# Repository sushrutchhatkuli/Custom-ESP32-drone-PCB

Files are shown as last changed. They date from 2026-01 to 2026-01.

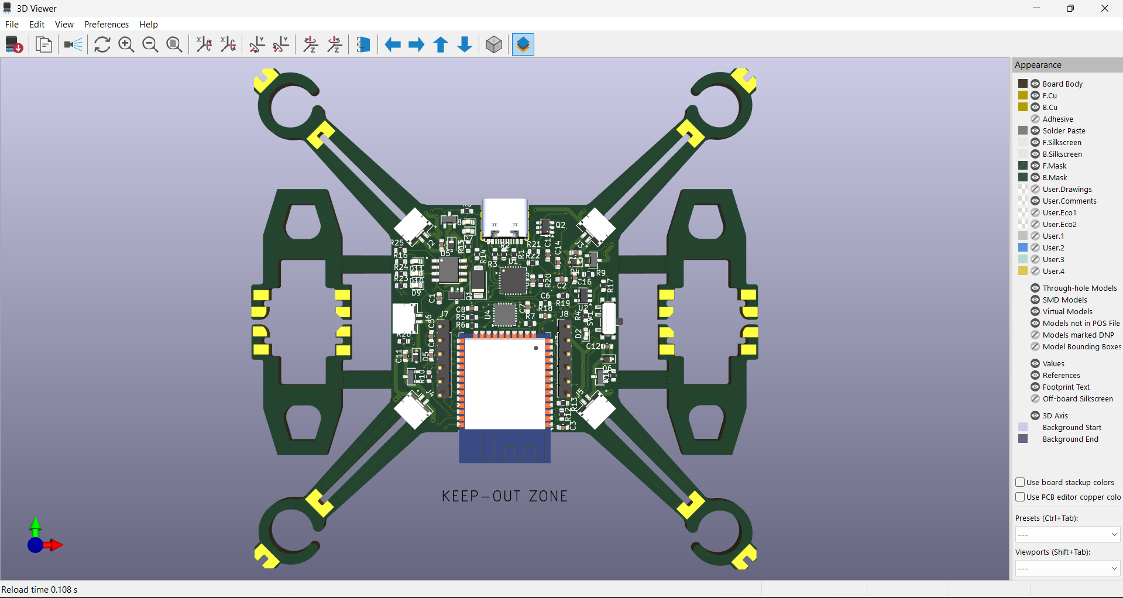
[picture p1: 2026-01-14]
Images/PCB Editor / 3D Views/Screenshot 2026-01-11 161916.png

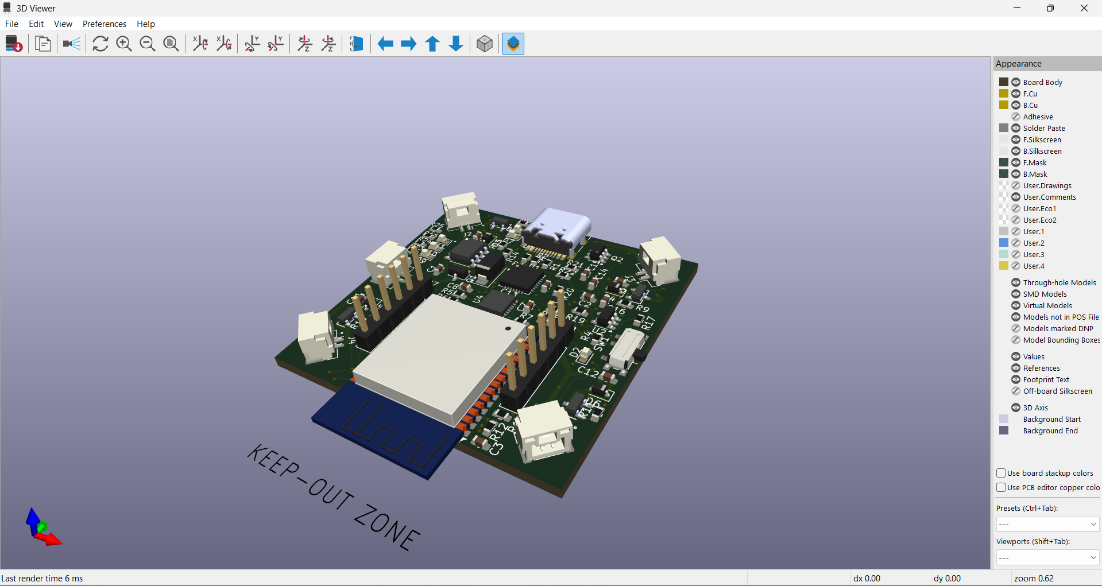
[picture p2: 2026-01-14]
Images/PCB Editor / 3D Views/Screenshot 2026-01-07 224814.png

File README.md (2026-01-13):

# Cheap Drone

I designed a custom drone flight controller PCB based on the ESP32-WROOM-32. The board uses USB-C charging, regulated 3.3 V power delivery, and onboard IMU sensing using the MPU-6050. The PCB is currently being fabricated, and I am actively working on automatic stabilization code for my motors.

## Overview
The goal of this project was to design a low-cost, custom flight controller PCB for a quadcopter drone while gaining hands-on experience with power management, embedded hardware design, and PCB layout. Instead of using a real controller, I wanted to use a free app that can be downloaded from the App store since ESP32 supports Wifi and Bluetooth.

The design is organized into three main parts:
- Power management
- ESP32 control and programming
- Motors and sensors

## Power Management
Power management was a major focus of this design. The board uses a battery charging circuit along with a voltage regulator to safely power all components. The incoming voltage is regulated to 3.3 V using the MIC5219-3.3YM5, which supplies power to both the ESP32 and the MPU-6050.

When the board is connected to USB-C, the voltage passes through a Schottky diode (SS34) and reaches the gate of an AO3401A P-channel MOSFET. This turns the MOSFET off and disconnects the battery (+VBatt) from the system, allowing the drone to run directly from USB power while the battery is charging.

Battery charging is handled by the TP4056, which safely manages the LiPo charging process. Two LEDs connected to the TP4056 indicate whether the battery is charging or fully charged. When the USB cable is unplugged, the MOSFET automatically turns on, reconnecting the battery so it can power the system. Decoupling capacitors are placed throughout the power rails to reduce noise and improve voltage stability.

## ESP32 Control and Programming
The +VBUS line is routed before the voltage regulator so it can supply 5 V power to the CP2102 USB-to-UART converter, which requires a higher voltage than the ESP32.

The USB data lines (D+ and D−) carry compiled code from the computer to the CP2102. The CP2102 converts this USB data into UART signals (TX and RX) that are sent to the ESP32. The RTS and DTR signals from the CP2102 pass through a 2N7002DW MOSFET, which automatically controls the EN and BOOT pins of the ESP32 during programming. This allows the ESP32 to enter firmware upload mode automatically and return to normal operation later without manual button presses.

The ESP32 acts as the main controller of the drone. It processes sensor data, controls motor outputs, and manages the overall behavior of the system. Orientation data from the MPU-6050 is used to adjust motor speeds for stabilization. I also added a UART2 (RXD2/TXD2) connector for future expansion and a four-channel SRV connector for motor control signals. Decoupling capacitors here on the 3.3 V rail help minimize noise from switching components.

## Motors and Sensors
The MPU-6050 is used as a 6-axis IMU to measure acceleration and angular velocity. It communicates with the ESP32 over I²C using the SDA and SCL lines, with pull-up resistors included to ensure reliable communication. The sensor operates at 3.3 V and is powered from the regulated supply.

The MPU-6050 does not control the motors directly. Instead, it sends motion data to the ESP32, which determines how each motor should respond to keep the drone stable. The motors are powered directly from the battery (+VBatt) because they require higher current than the logic circuitry.

Each motor is driven using an SI2302 N-channel MOSFET, allowing low-power control signals from the ESP32 to switch high-current motor loads. The MOSFET gates are driven by the ESP32, the sources are connected to ground, and the drains connect to the motors and battery supply. Since motors generate voltage spikes when switching, flyback diodes are included to protect the MOSFETs and surrounding components.

## Current Status
- Schematic and PCB design completed
- All ERC and DRC checks passed
- PCB fabrication and soldering the components in progress
- Automatic stabilization firmware under development

## Future Work
- Adding object-tracking cameras
- 3D Mapping using SLAM
- Perform flight testing and tuning
- Rev B PCB improvements based on test results

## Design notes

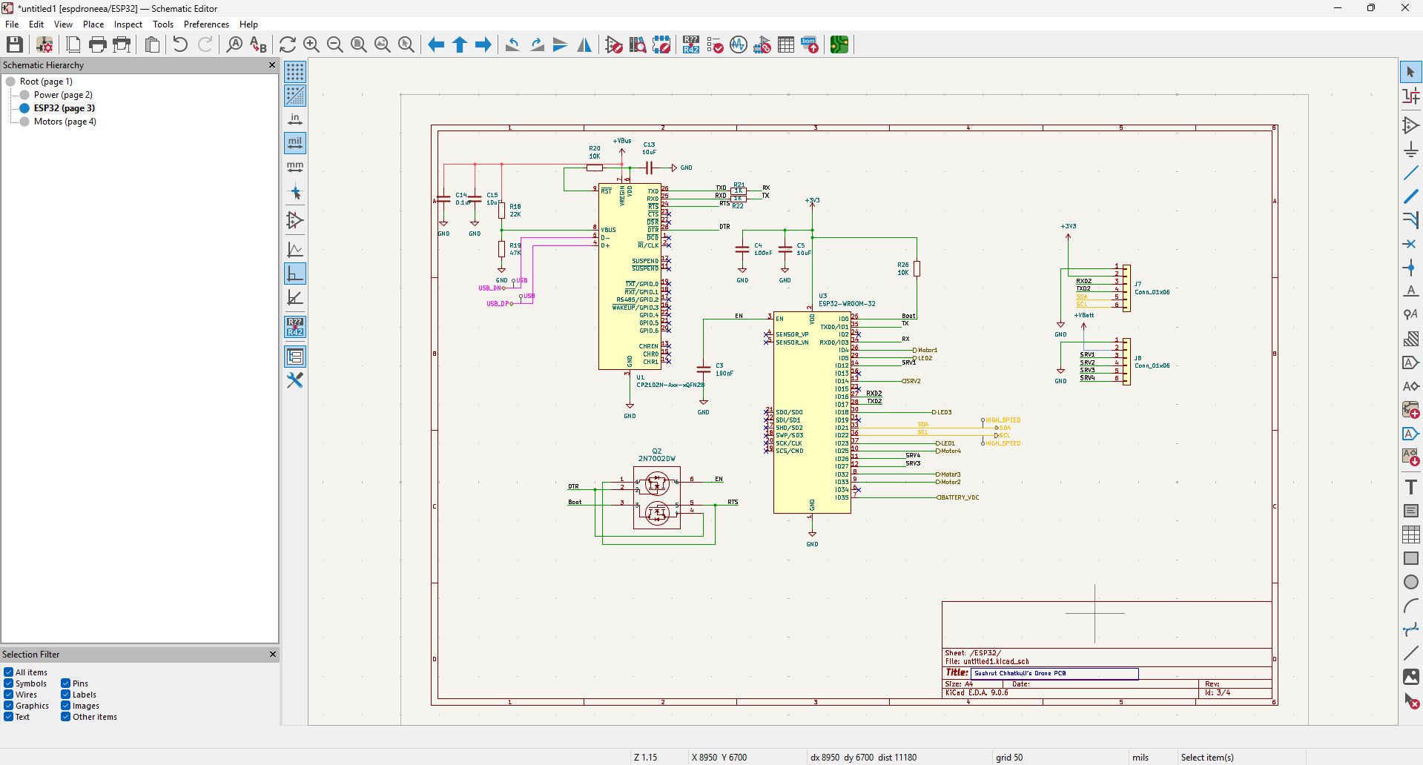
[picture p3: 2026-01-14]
Images/schematics/Screenshot 2026-01-14 183303.png

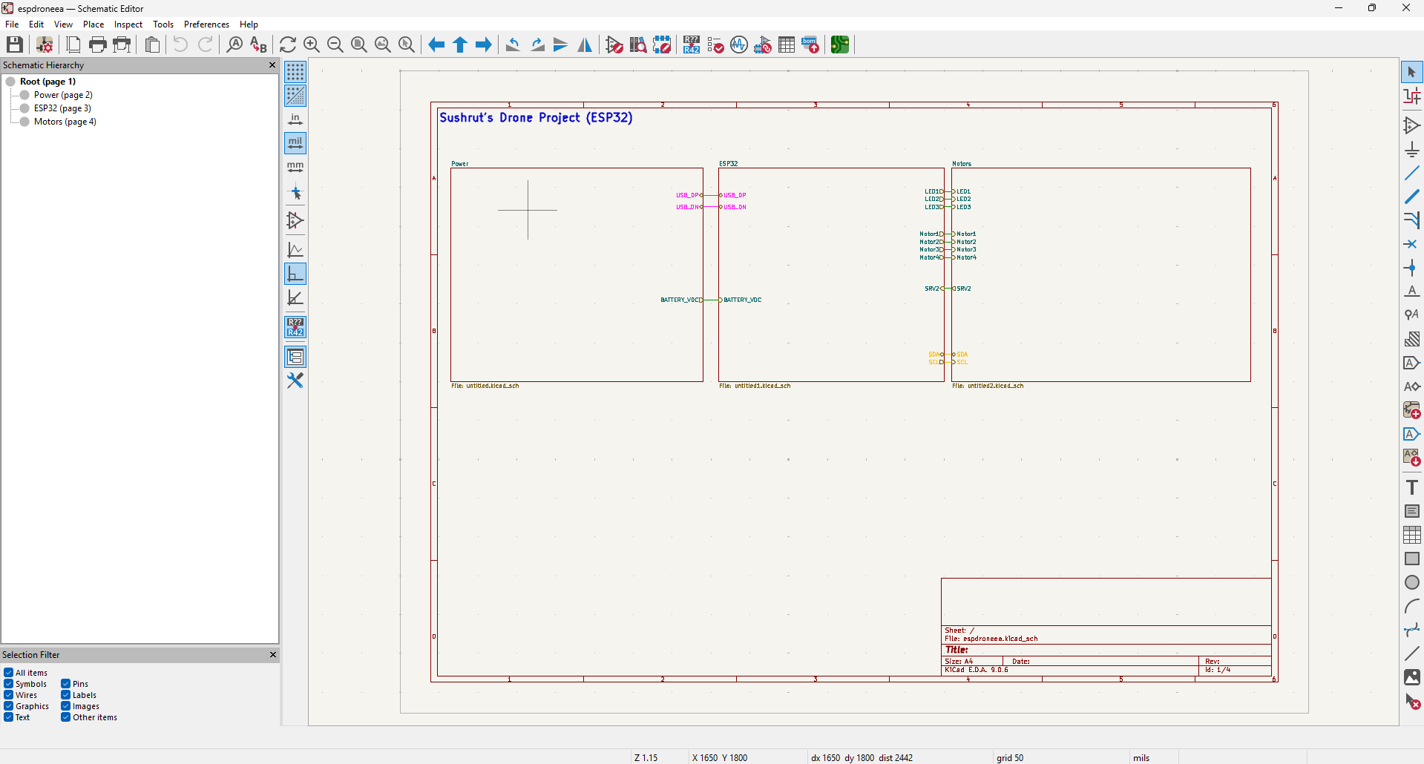
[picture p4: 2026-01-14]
Images/schematics/Screenshot 2026-01-14 162815.png

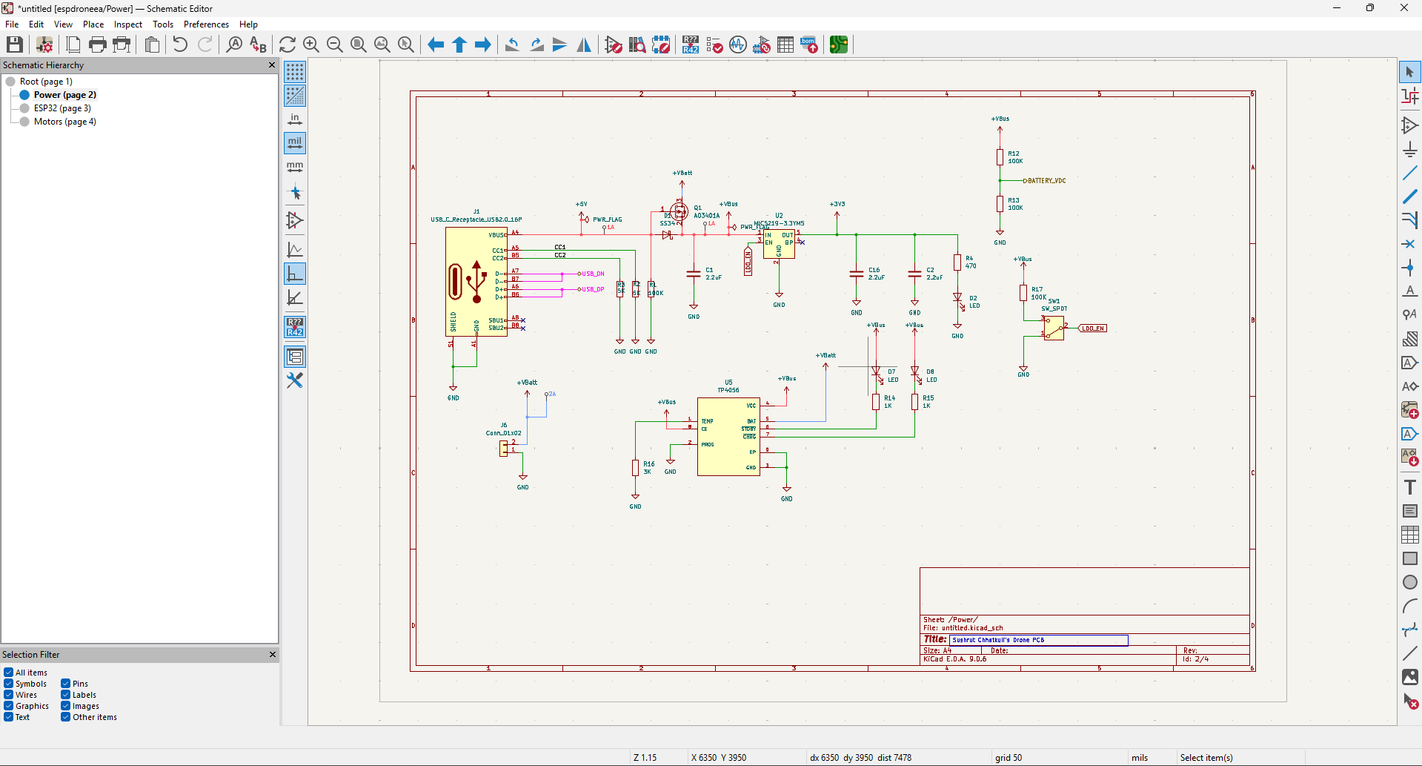
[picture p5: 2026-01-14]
Images/schematics/Screenshot 2026-01-14 183249.png

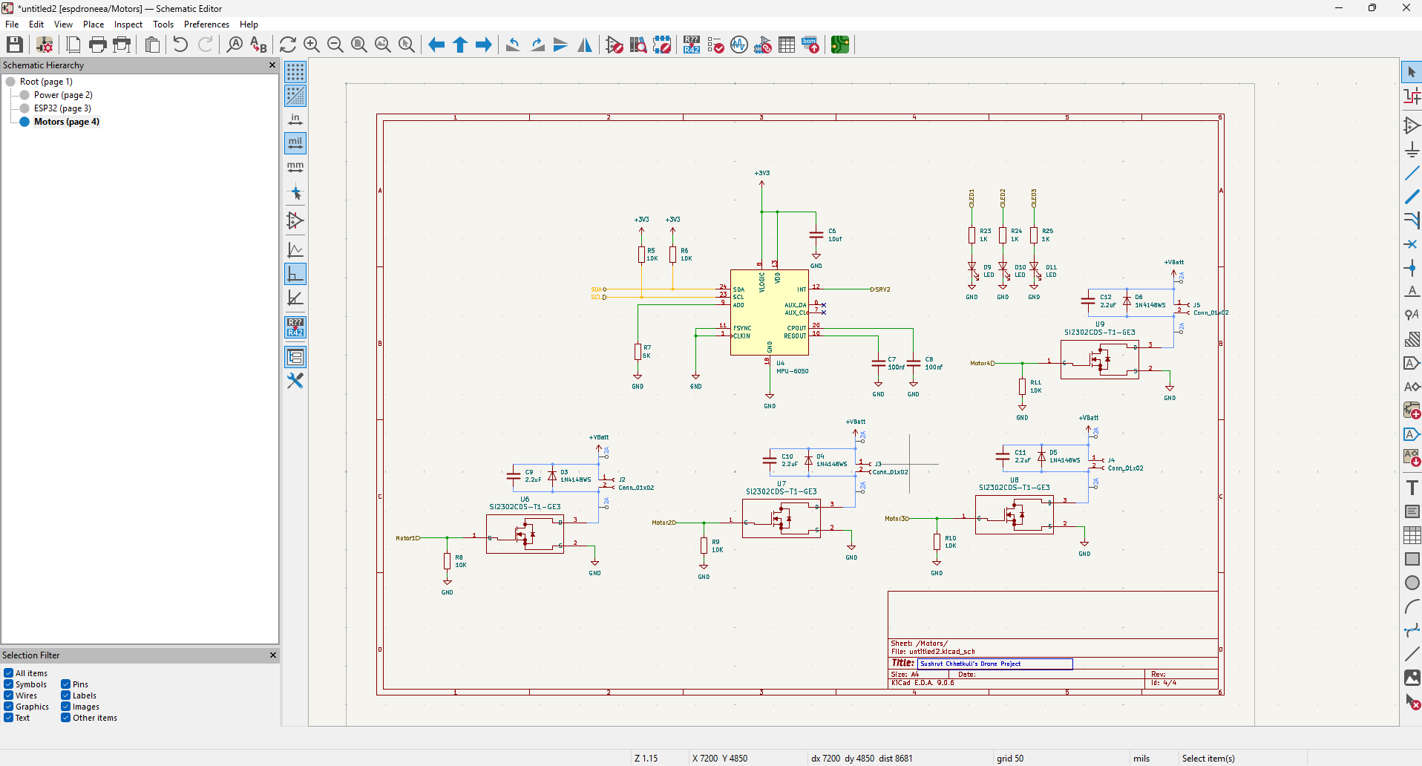
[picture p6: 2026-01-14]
Images/schematics/Screenshot 2026-01-14 183317.png

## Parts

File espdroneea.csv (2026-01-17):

# | Reference | Qty | Value | DNP | Exclude from BOM | Exclude from Board | Footprint | Datasheet
1 | C1,C2,C9,C10,C11,C12,C16 | 7 | 2.2uF |  |  |  | Capacitor_SMD:C_0603_1608Metric | ~
2 | C3,C4 | 2 | 100nF |  |  |  | Capacitor_SMD:C_0603_1608Metric | ~
3 | C5,C13,C15 | 3 | 10uF |  |  |  | Capacitor_SMD:C_0603_1608Metric | ~
4 | C6 | 1 | 10uf |  |  |  | Capacitor_SMD:C_0603_1608Metric | ~
5 | C7,C8 | 2 | 100nf |  |  |  | Capacitor_SMD:C_0603_1608Metric | ~
6 | C14 | 1 | 0.1uF |  |  |  | Capacitor_SMD:C_0603_1608Metric | ~
7 | D1 | 1 | SS34 |  |  |  | Diode_SMD:D_SMA | https://www.vishay.com/docs/88751/ss32.pdf
8 | D2,D7,D8,D9,D10,D11 | 6 | LED |  |  |  | LED_SMD:LED_0603_1608Metric | ~
9 | D3,D4,D5,D6 | 4 | 1N4148WS |  |  |  | Diode_SMD:D_SOD-323 | https://www.vishay.com/docs/85751/1n4148ws.pdf
10 | J1 | 1 | USB_C_Receptacle_USB2.0_16P |  |  |  | DroneProject:USB_C_Receptacle_HRO_TYPE-C-31-M-12 | https://www.usb.org/sites/default/files/documents/usb_type-c.zip
11 | J2,J3,J4,J5,J6 | 5 | Conn_01x02 |  |  |  | Connector_JST:JST_GH_SM02B-GHS-TB_1x02-1MP_P1.25mm_Horizontal | ~
12 | J7,J8 | 2 | Conn_01x06 |  |  |  | Connector_PinHeader_2.54mm:PinHeader_1x06_P2.54mm_Vertical | ~
13 | Q1 | 1 | AO3401A |  |  |  | Package_TO_SOT_SMD:SOT-23 | http://www.aosmd.com/pdfs/datasheet/AO3401A.pdf
14 | Q2 | 1 | 2N7002DW |  |  |  | Package_TO_SOT_SMD:SOT-23-6
15 | R1,R12,R13,R17 | 4 | 100K |  |  |  | Resistor_SMD:R_0603_1608Metric | ~
16 | R2,R3,R7 | 3 | 5K |  |  |  | Resistor_SMD:R_0603_1608Metric | ~
17 | R4 | 1 | 470 |  |  |  | Resistor_SMD:R_0603_1608Metric | ~
18 | R5,R6,R8,R9,R10,R11,R20,R26 | 8 | 10K |  |  |  | Resistor_SMD:R_0603_1608Metric | ~
19 | R14,R15,R21,R22,R23,R24,R25 | 7 | 1K |  |  |  | Resistor_SMD:R_0603_1608Metric | ~
20 | R16 | 1 | 3K |  |  |  | Resistor_SMD:R_0603_1608Metric | ~
21 | R18 | 1 | 22K |  |  |  | Resistor_SMD:R_0603_1608Metric | ~
22 | R19 | 1 | 47K |  |  |  | Resistor_SMD:R_0603_1608Metric | ~
23 | SW1 | 1 | SW_SPDT |  |  |  | Button_Switch_SMD:SW_SPDT_PCM12 | ~
24 | U1 | 1 | CP2102N-Axx-xQFN28 |  |  |  | Package_DFN_QFN:QFN-28-1EP_5x5mm_P0.5mm_EP3.35x3.35mm | https://www.silabs.com/documents/public/data-sheets/cp2102n-datasheet.pdf
25 | U2 | 1 | MIC5219-3.3YM5 |  |  |  | Package_TO_SOT_SMD:SOT-23-5 | http://ww1.microchip.com/downloads/en/DeviceDoc/MIC5219-500mA-Peak-Output-LDO-Regulator-DS20006021A.pdf
26 | U3 | 1 | ESP32-WROOM-32 |  |  |  | RF_Module:ESP32-WROOM-32 | https://www.espressif.com/sites/default/files/documentation/esp32-wroom-32_datasheet_en.pdf
27 | U4 | 1 | MPU-6050 |  |  |  | Sensor_Motion:InvenSense_QFN-24_4x4mm_P0.5mm | https://invensense.tdk.com/wp-content/uploads/2015/02/MPU-6000-Datasheet1.pdf
28 | U5 | 1 | TP4056 |  |  |  | DroneProject:SOP127P600X175-9N
29 | U6,U7,U8,U9 | 4 | SI2302CDS-T1-GE3 |  |  |  | DroneProject:TO-236_VIS

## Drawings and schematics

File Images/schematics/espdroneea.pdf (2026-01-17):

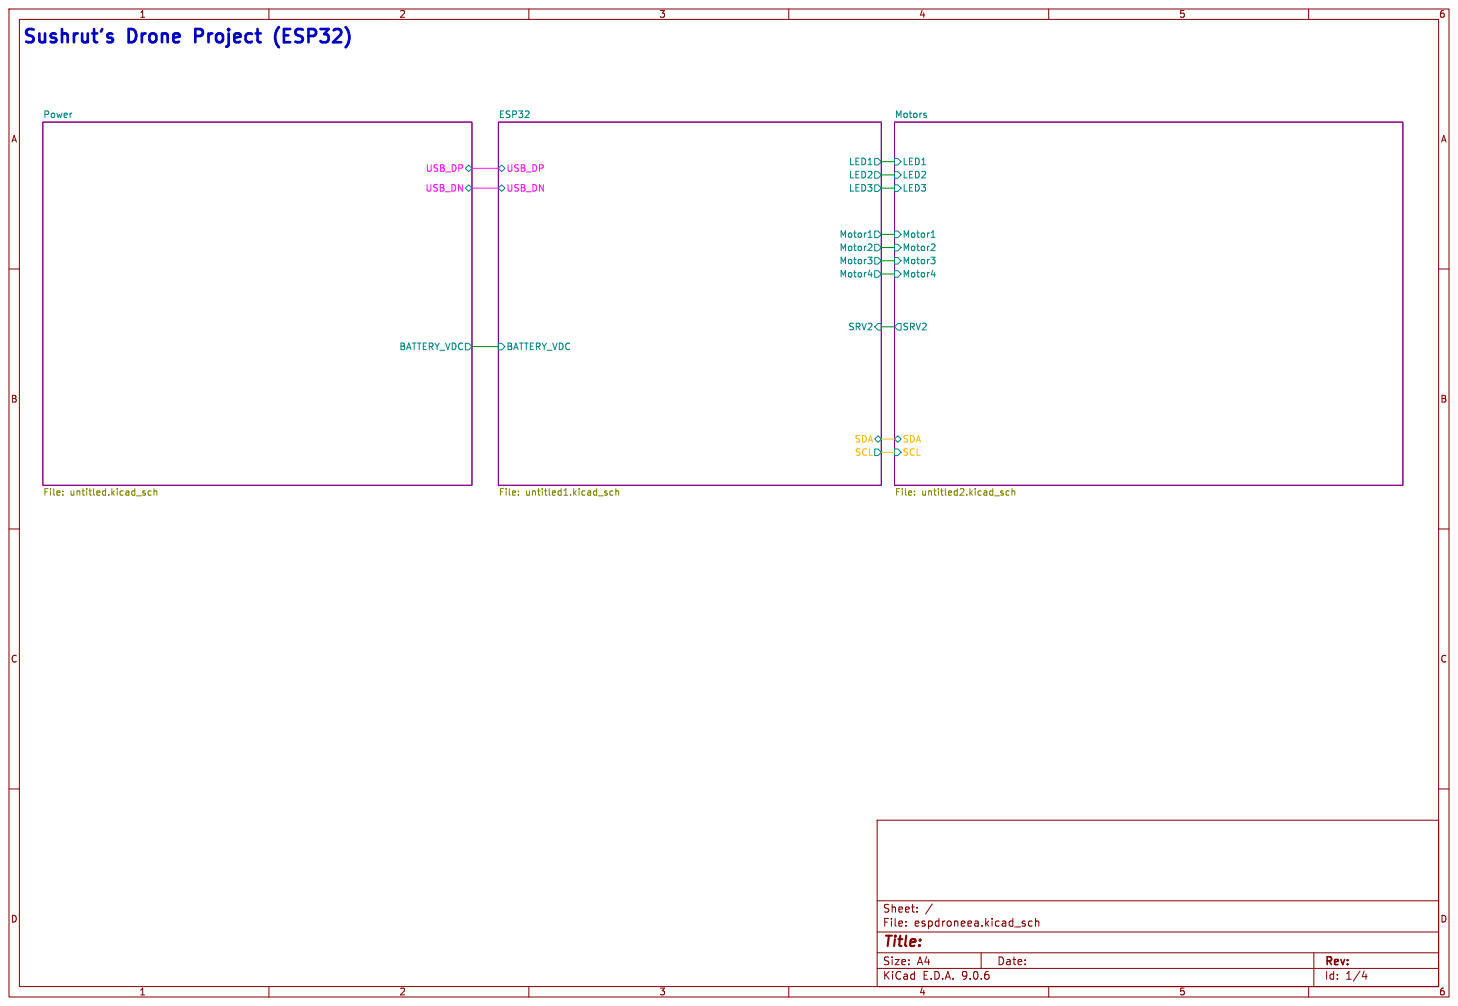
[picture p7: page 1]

Id: 1/4 Title: File: espdroneea.kicad_sch Sheet: /

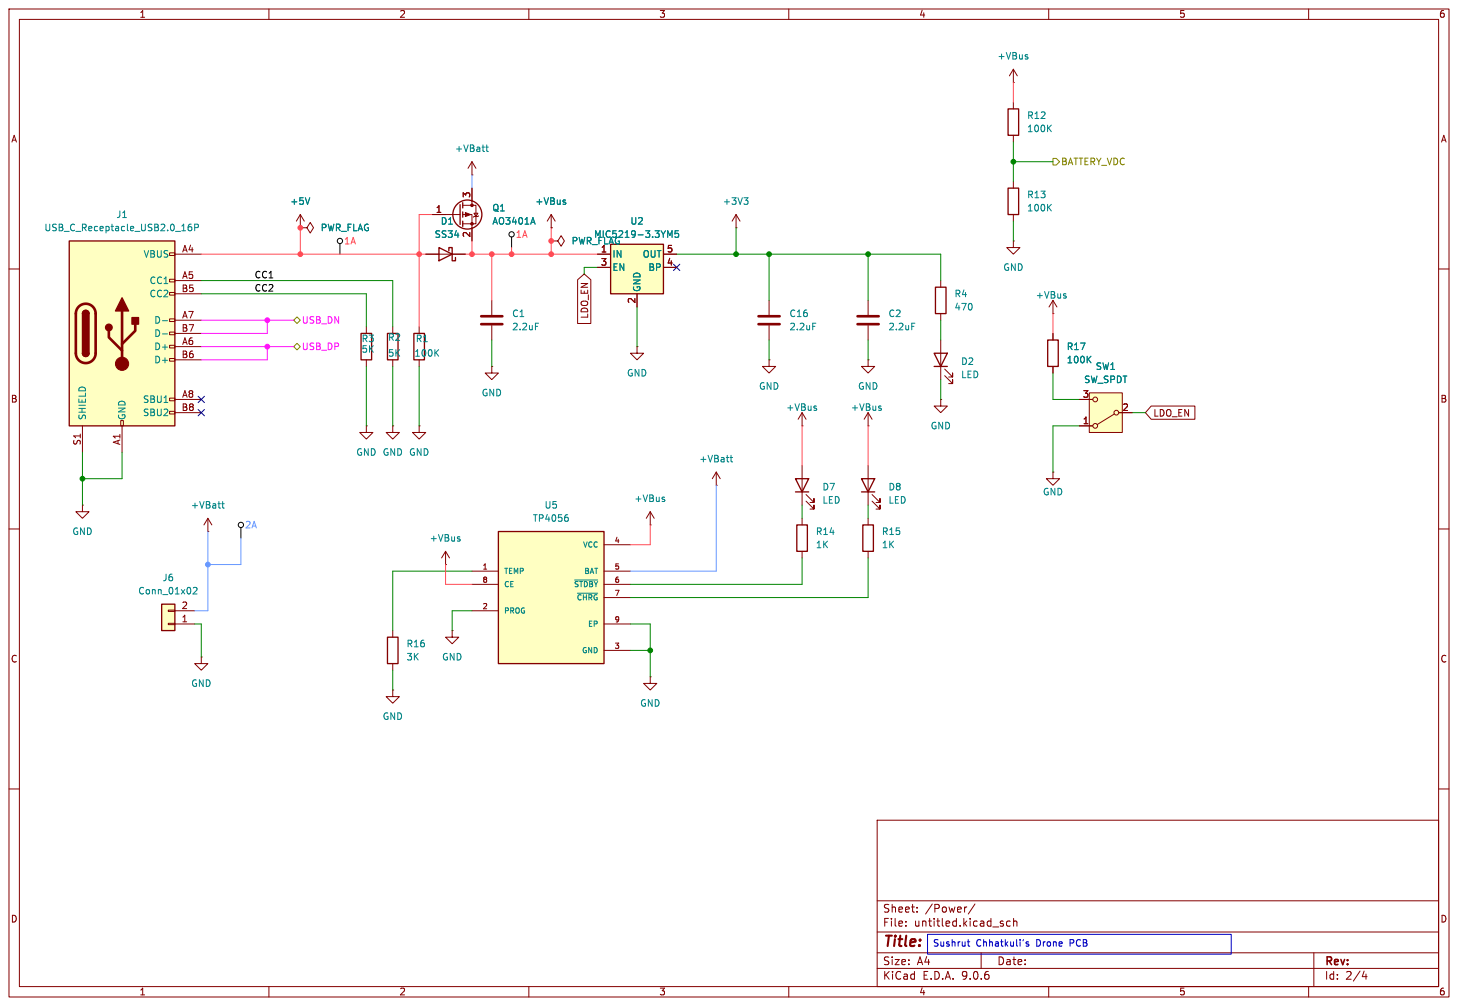
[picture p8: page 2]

2 OUT 5 BP 4 U2 MIC5219-3.3YM5 GND GND

Id: 2/4 Title: File: untitled.kicad_sch Sheet: /Power/ GND

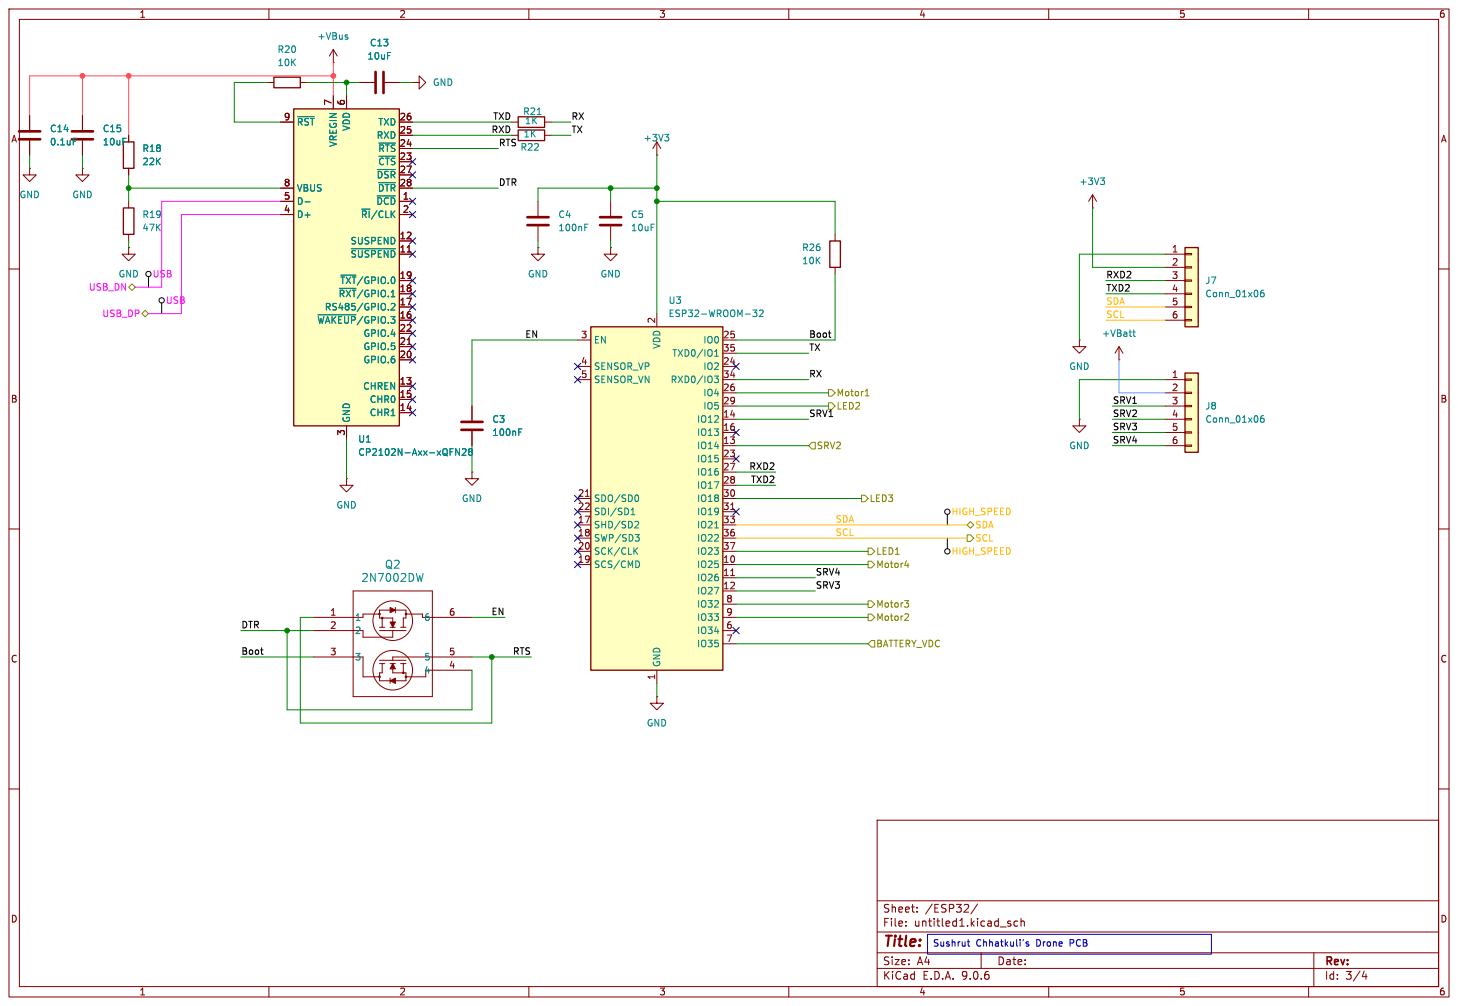
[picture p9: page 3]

3 TXD 26 RXD 25 ~{RTS} 24 ~{CTS} 23 ~{DSR} 27 ~{DTR} 28 ~{DCD}1 ~{RI}/CLK2 SUSPEND 12 ~{SUSPEND}11 ~{TXT}/GPIO.019 ~{RXT}/GPIO.118 RS485/GPIO.2 17 ~{WAKEUP}/GPIO.316 GPIO.4 22 GPIO.5 21 GPIO.6 20 CHREN 13 CHR0 15 CHR1 14 U1 CP2102N-Axx-xQFN28 GND

3 TXD 26 RXD 25 ~{RTS} 24 ~{CTS} 23 ~{DSR} 27 ~{DTR} 28 ~{DCD}1 ~{RI}/CLK2 SUSPEND 12 ~{SUSPEND}11 ~{TXT}/GPIO.019 ~{RXT}/GPIO.118 RS485/GPIO.2 17 ~{WAKEUP}/GPIO.316 GPIO.4 22 GPIO.5 21 GPIO.6 20 CHREN 13 CHR0 15 CHR1 14 C3

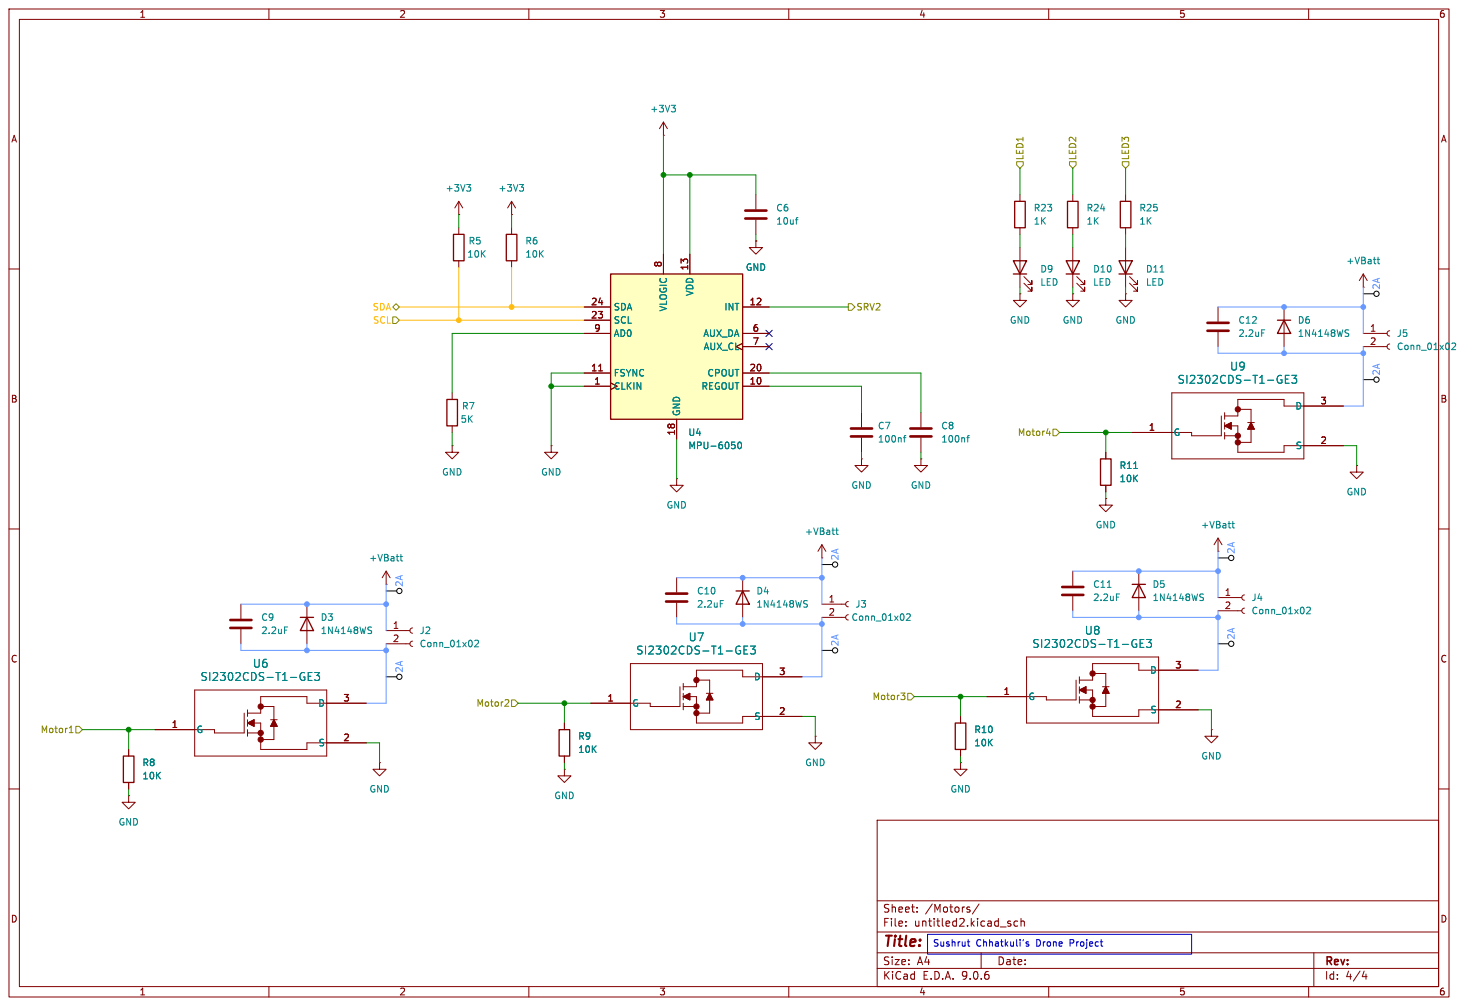
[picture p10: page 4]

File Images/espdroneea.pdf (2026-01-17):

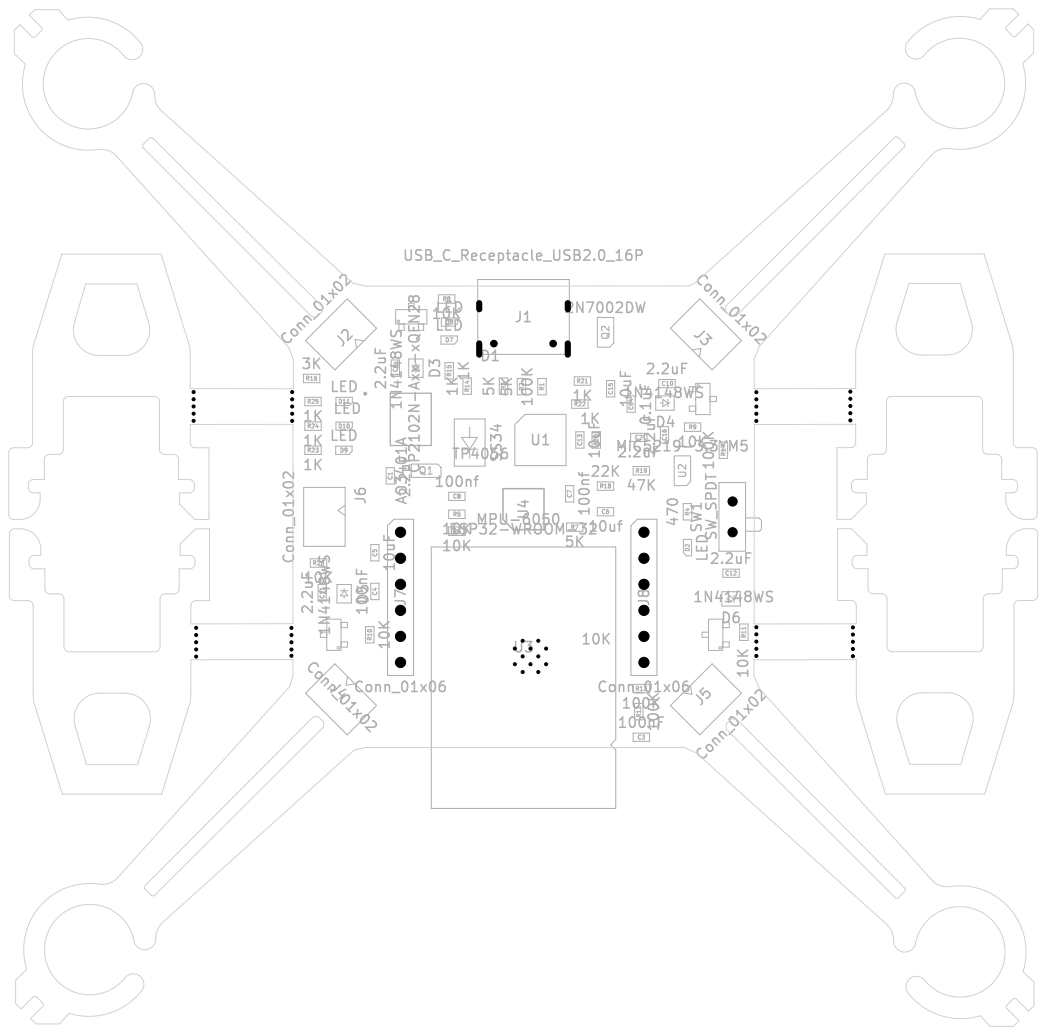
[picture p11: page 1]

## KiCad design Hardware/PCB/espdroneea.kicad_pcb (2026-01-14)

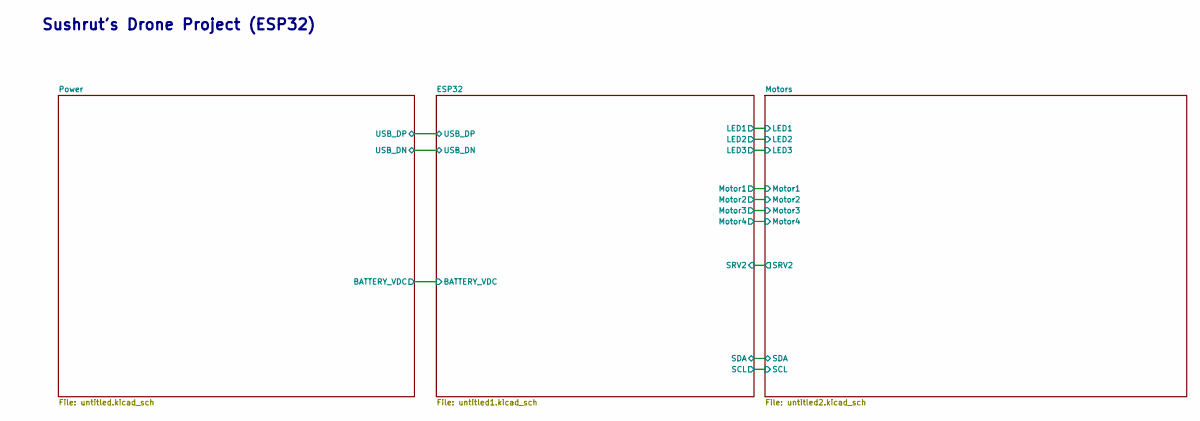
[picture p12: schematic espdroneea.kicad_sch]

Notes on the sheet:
Sushrut's Drone Project (ESP32)

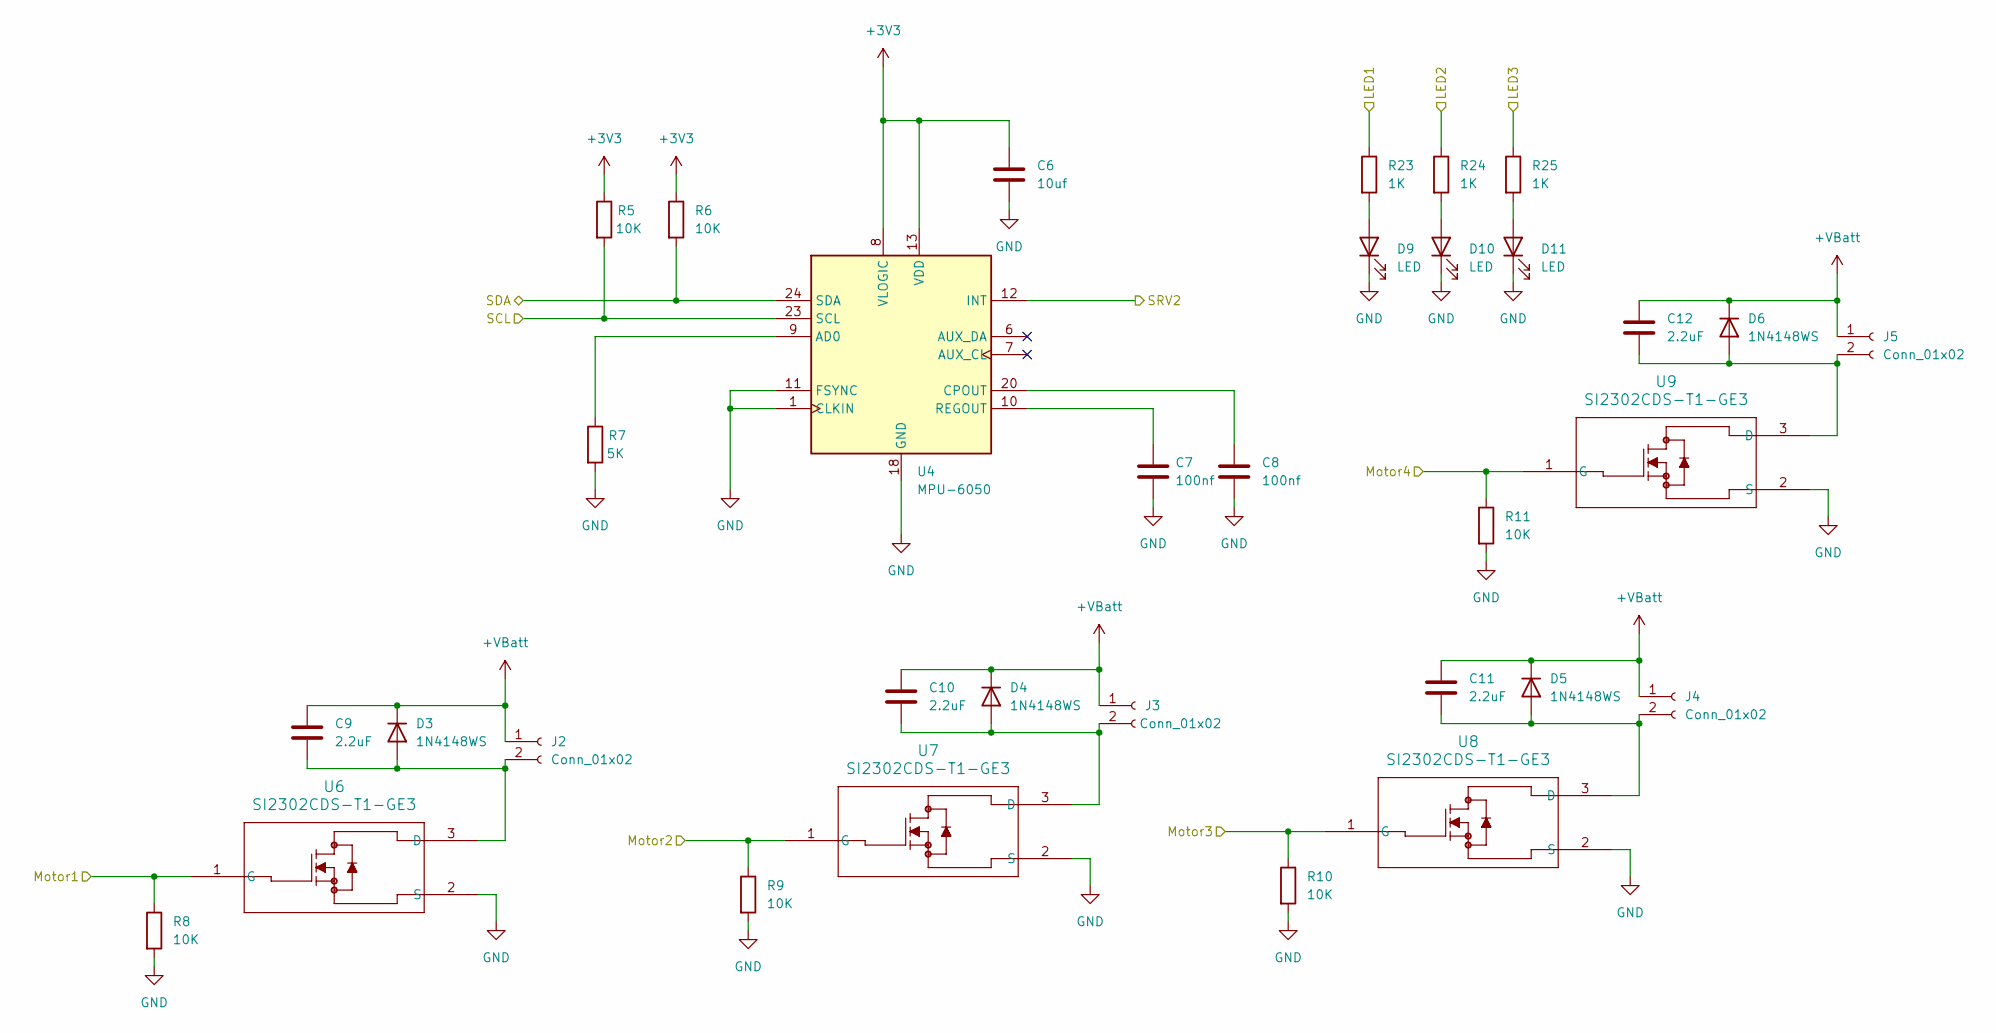
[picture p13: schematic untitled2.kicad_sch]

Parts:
C6: 10uf; C_0603_1608Metric
C7, C8: 100nf; C_0603_1608Metric
C9, C10, C11, C12: 2.2uF; C_0603_1608Metric
D3, D4, D5, D6: 1N4148WS; D_SOD-323
D9, D10, D11: LED; LED_0603_1608Metric
J2, J3, J4, J5: Conn_01x02; JST_GH_SM02B-GHS-TB_1x02-1MP_P1.25mm_Horizontal
R5, R6, R8, R9, R10, R11: 10K; R_0603_1608Metric
R7: 5K; R_0603_1608Metric
R23, R24, R25: 1K; R_0603_1608Metric
U4: MPU-6050; InvenSense_QFN-24_4x4mm_P0.5mm
U6, U7, U8, U9: SI2302CDS-T1-GE3; TO-236_VIS

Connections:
+3V3: C6.1, R5.1, R6.1, U4.8 (VLOGIC), U4.13 (VDD); also elsewhere on the board
+VBatt: C9.1, C10.1, C11.1, C12.1, D3.1 (K), D4.1 (K), D5.1 (K), D6.1 (K), J2.1, J3.1, J4.1, J5.1; also elsewhere on the board
/ESP32/LED1: R23.1; also elsewhere on the board
/ESP32/LED2: R24.1; also elsewhere on the board
/ESP32/LED3: R25.1; also elsewhere on the board
/ESP32/Motor1: R8.1, U6.1 (G); also elsewhere on the board
/ESP32/Motor2: R9.1, U7.1 (G); also elsewhere on the board
/ESP32/Motor3: R10.1, U8.1 (G); also elsewhere on the board
/ESP32/Motor4: R11.1, U9.1 (G); also elsewhere on the board
/ESP32/SCL: R5.2, U4.23 (SCL); also elsewhere on the board
/ESP32/SDA: R6.2, U4.24 (SDA); also elsewhere on the board
/ESP32/SRV2: U4.12 (INT); also elsewhere on the board
GND: C6.2, C7.2, C8.2, D9.1 (K), D10.1 (K), D11.1 (K), R7.2, R8.2, R9.2, R10.2, R11.2, U4.1 (CLKIN), U4.11 (FSYNC), U4.18 (GND), U6.2 (S), U7.2 (S), U8.2 (S), U9.2 (S); also elsewhere on the board
unnamed: C9.2, D3.2 (A), J2.2, U6.3 (D)
unnamed: C10.2, D4.2 (A), J3.2, U7.3 (D)
unnamed: C11.2, D5.2 (A), J4.2, U8.3 (D)
unnamed: C12.2, D6.2 (A), J5.2, U9.3 (D)
unnamed: D9.2 (A), R23.2
unnamed: D10.2 (A), R24.2
unnamed: D11.2 (A), R25.2
unnamed: R7.1, U4.9 (AD0)
unnamed: C8.1, U4.20 (CPOUT)
unnamed: C7.1, U4.10 (REGOUT)

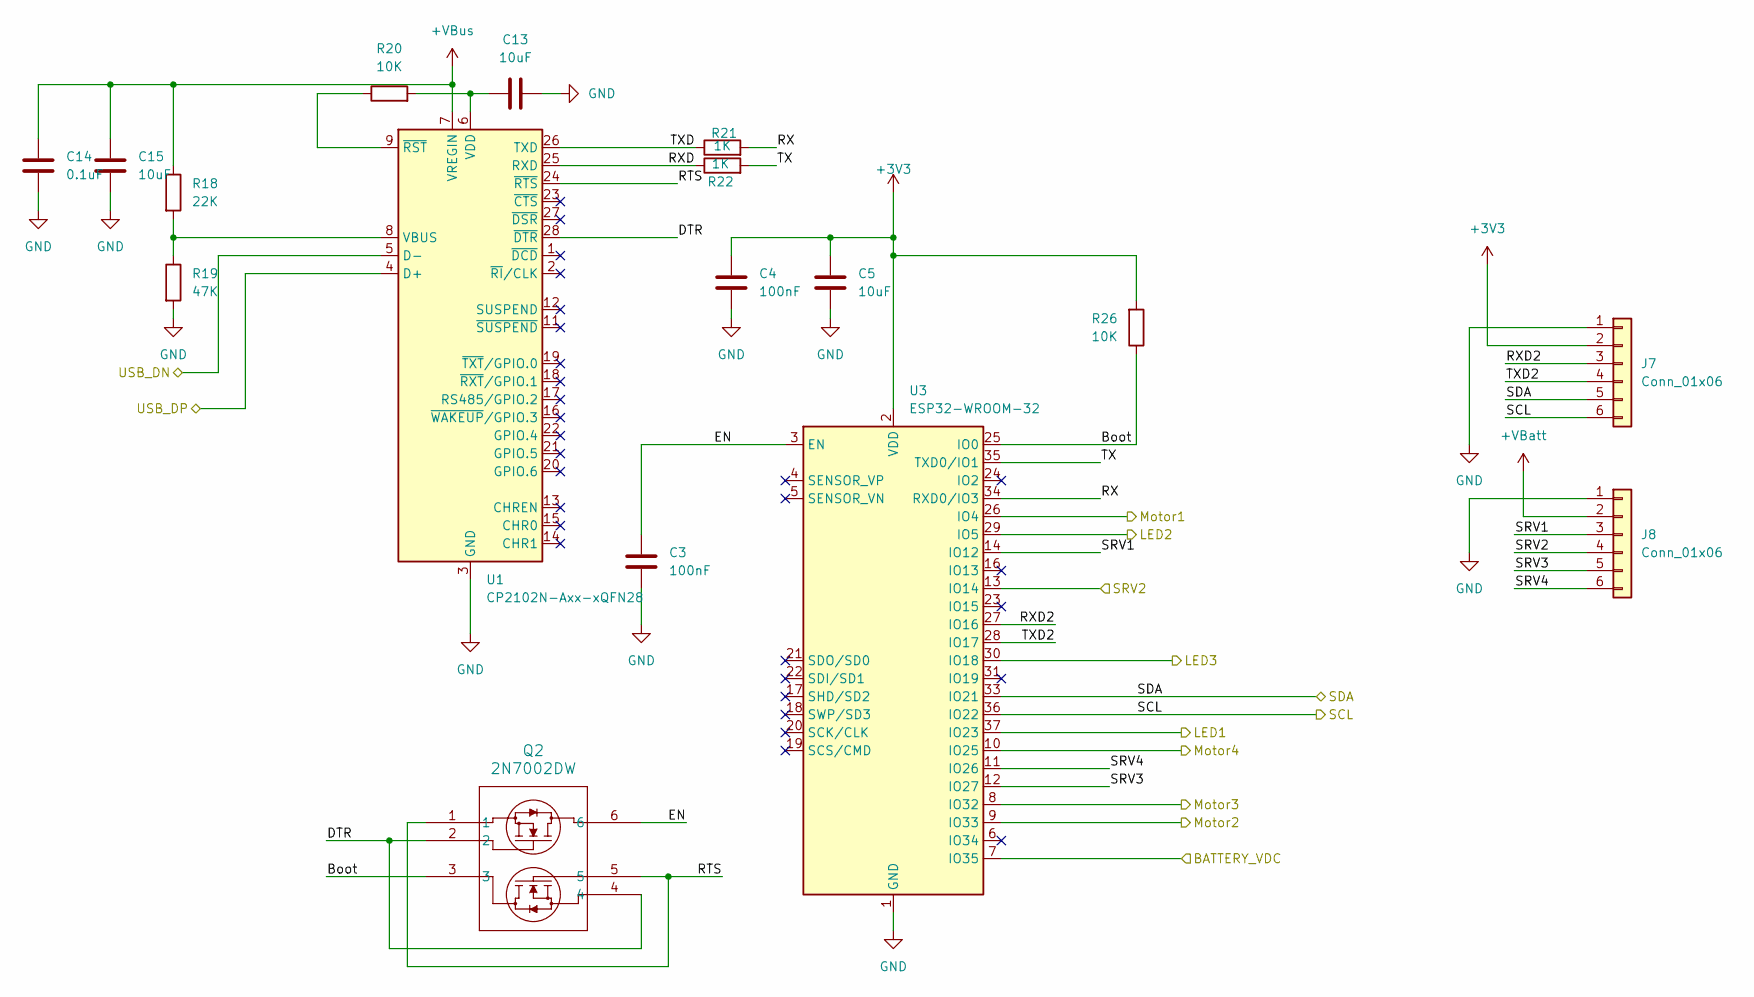
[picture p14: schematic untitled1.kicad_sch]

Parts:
C3, C4: 100nF; C_0603_1608Metric
C5, C13, C15: 10uF; C_0603_1608Metric
C14: 0.1uF; C_0603_1608Metric
J7, J8: Conn_01x06; PinHeader_1x06_P2.54mm_Vertical
Q2: 2N7002DW; SOT-23-6
R18: 22K; R_0603_1608Metric
R19: 47K; R_0603_1608Metric
R20, R26: 10K; R_0603_1608Metric
R21, R22: 1K; R_0603_1608Metric
U1: CP2102N-Axx-xQFN28; QFN-28-1EP_5x5mm_P0.5mm_EP3.35x3.35mm
U3: ESP32-WROOM-32

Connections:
+3V3: C4.1, C5.1, J7.2, R26.2, U3.2 (VDD); also elsewhere on the board
+VBatt: J8.2; also elsewhere on the board
+VBus: C14.1, C15.1, R18.1, U1.7 (VREGIN); also elsewhere on the board
/ESP32/BATTERY_VDC: U3.7 (IO35); also elsewhere on the board
/ESP32/Boot: Q2.3, R26.1, U3.25 (IO0)
/ESP32/DTR: Q2.2, Q2.4, U1.28 (~DTR)
/ESP32/EN: C3.1, Q2.6, U3.3 (EN)
/ESP32/LED1: U3.37 (IO23); also elsewhere on the board
/ESP32/LED2: U3.29 (IO5); also elsewhere on the board
/ESP32/LED3: U3.30 (IO18); also elsewhere on the board
/ESP32/Motor1: U3.26 (IO4); also elsewhere on the board
/ESP32/Motor2: U3.9 (IO33); also elsewhere on the board
/ESP32/Motor3: U3.8 (IO32); also elsewhere on the board
/ESP32/Motor4: U3.10 (IO25); also elsewhere on the board
/ESP32/RTS: Q2.1, Q2.5, U1.24 (~RTS)
/ESP32/RX: R21.2, U3.34 (RXD0/IO3)
/ESP32/RXD: R22.1, U1.25 (RXD)
/ESP32/RXD2: J7.3, U3.27 (IO16)
/ESP32/SCL: J7.6, U3.36 (IO22); also elsewhere on the board
/ESP32/SDA: J7.5, U3.33 (IO21); also elsewhere on the board
/ESP32/SRV1: J8.3, U3.14 (IO12)
/ESP32/SRV2: J8.4, U3.13 (IO14); also elsewhere on the board
/ESP32/SRV3: J8.5, U3.12 (IO27)
/ESP32/SRV4: J8.6, U3.11 (IO26)
/ESP32/TX: R22.2, U3.35 (TXD0/IO1)
/ESP32/TXD: R21.1, U1.26 (TXD)
/ESP32/TXD2: J7.4, U3.28 (IO17)
/ESP32/USB_DN: U1.5 (D-); also elsewhere on the board
/ESP32/USB_DP: U1.4 (D+); also elsewhere on the board
GND: C3.2, C4.2, C5.2, C13.2, C14.2, C15.2, J7.1, J8.1, R19.2, U1.3 (GND), U1.29 (GND), U3.1 (GND), U3.15 (GND), U3.38 (GND), U3.39 (GND); also elsewhere on the board
unnamed: R18.2, R19.1, U1.8 (VBUS)
unnamed: C13.1, R20.2, U1.6 (VDD)
unnamed: R20.1, U1.9 (~RST)

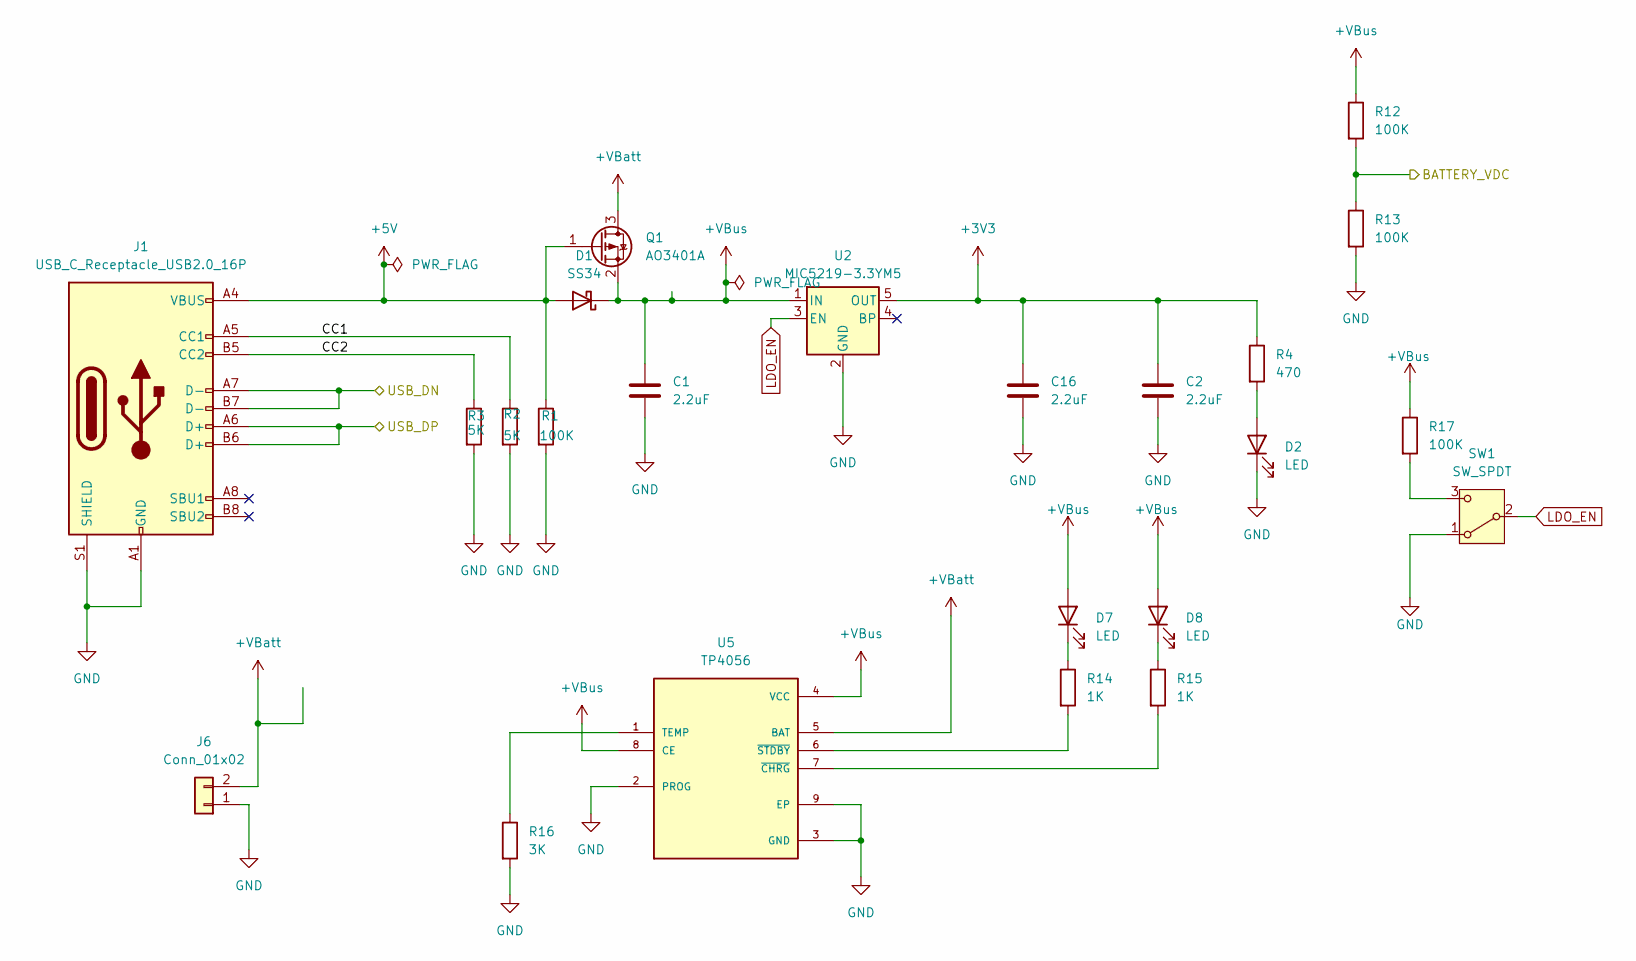
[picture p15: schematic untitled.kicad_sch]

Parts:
C1, C2, C16: 2.2uF; C_0603_1608Metric
D1: SS34; D_SMA
D2, D7, D8: LED; LED_0603_1608Metric
J1: USB_C_Receptacle_USB2.0_16P; USB_C_Receptacle_HRO_TYPE-C-31-M-12
J6: Conn_01x02; JST_GH_SM02B-GHS-TB_1x02-1MP_P1.25mm_Horizontal
Q1: AO3401A; SOT-23
R1, R12, R13, R17: 100K; R_0603_1608Metric
R2, R3: 5K; R_0603_1608Metric
R4: 470; R_0603_1608Metric
R14, R15: 1K; R_0603_1608Metric
R16: 3K; R_0603_1608Metric
SW1: SW_SPDT; SW_SPDT_PCM12
U2: MIC5219-3.3YM5; SOT-23-5
U5: TP4056; SOP127P600X175-9N

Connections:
+3V3: C2.1, C16.1, R4.1, U2.5 (OUT); also elsewhere on the board
+5V: D1.2 (A), J1.A4 (VBUS), J1.A9 (VBUS), J1.B4 (VBUS), J1.B9 (VBUS), Q1.1 (G), R1.1
+VBatt: J6.2, Q1.3 (D), U5.5 (BAT); also elsewhere on the board
+VBus: C1.1, D1.1 (K), D7.2 (A), D8.2 (A), Q1.2 (S), R12.1, R17.1, U2.1 (IN), U5.4 (VCC), U5.8 (CE); also elsewhere on the board
/ESP32/BATTERY_VDC: R12.2, R13.1; also elsewhere on the board
/ESP32/USB_DN: J1.A7 (D-), J1.B7 (D-); also elsewhere on the board
/ESP32/USB_DP: J1.A6 (D+), J1.B6 (D+); also elsewhere on the board
/Power/CC1: J1.A5 (CC1), R2.1
/Power/CC2: J1.B5 (CC2), R3.1
GND: C1.2, C2.2, C16.2, D2.1 (K), J1.A1 (GND), J1.A12 (GND), J1.B1 (GND), J1.B12 (GND), J1.S1 (SHIELD), J6.1, R1.2, R2.2, R3.2, R13.2, R16.2, SW1.1 (A), U2.2 (GND), U5.2 (PROG), U5.3 (GND), U5.9 (EP); also elsewhere on the board
LDO_EN: SW1.2 (B), U2.3 (EN)
unnamed: D2.2 (A), R4.2
unnamed: D7.1 (K), R14.1
unnamed: D8.1 (K), R15.1
unnamed: R17.2, SW1.3 (C)
unnamed: R16.1, U5.1 (TEMP)
unnamed: R15.2, U5.7 (~CHRG)
unnamed: R14.2, U5.6 (~STDBY)

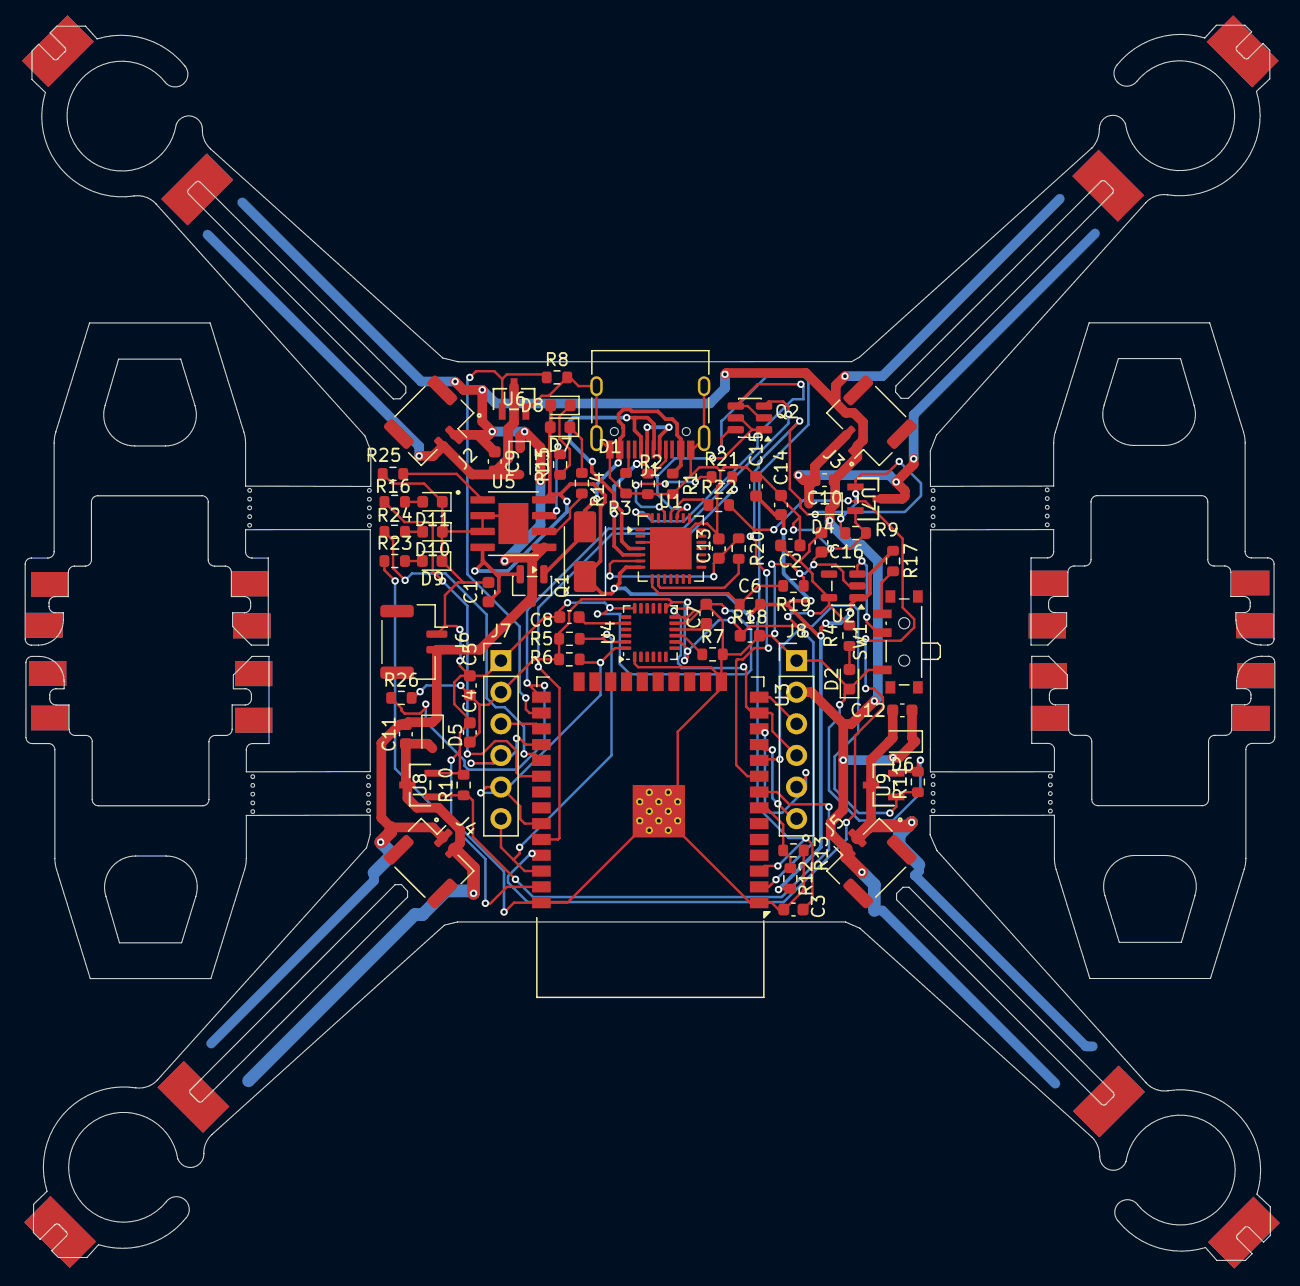
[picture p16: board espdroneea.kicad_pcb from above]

Board: 2 copper layers, 100.4 x 99.2 mm, 73 parts (0 on the bottom side), 54 nets.

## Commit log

2026-01-14 Create pcb
2026-01-14 Create footprints
2026-01-17 Add files via upload
    Bill of Materials (BOM)
    [espdroneea.csv]
